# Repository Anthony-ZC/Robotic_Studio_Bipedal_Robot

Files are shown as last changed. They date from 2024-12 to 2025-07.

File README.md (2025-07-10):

# Robot Studio: Bipeda Robot Full Project Implementation  
It is a bipedal robot implementation for **Columbia MECE 4611 Robotics Studio (Fall 2024)** created by ***Zewen "Anthony" Chen*** and ***Xinhe "Carl" Yang*** . We get inspiration by Yuhang Hu's work [CB-20](https://www.youtube.com/watch?v=Y0fBdpLf9ZI&t=1s) and redesign it.

---

### Say Beforehand

For those who attend Robotics Studio in the future or want to build their own first bipedal robot, I hope this implementation can help you. But remember, it is far from perfect. Here are drawbacks and suggestions for improvement:
1. It is relatively heavy, the whole weight reaches close to 1.5 kg. and the weight is not concentrated enough, if you can lighten it and concentrate the mass it should be able to run faster. I think under 1.2kg would be ideal.
2. The fact that we don't have the two motors located in the hip joints due to timing issues results in extra weight. If you can make the most of them, the robot should be able to make more gaits and be more stable.
3. Due to the parallel design of the legs, they are compressed by their own weight and can not be considered as rigid bodies, which makes simulation to reality more difficult, improving the design or replacing the other structures may improve.

### <u>**So, do not just copy it, make it better!**</u>  

Best wishes,  
Anthony Chen  

---

### Project Overview

- **Project Video**  
  - [x] Playlist Link: [https://www.youtube.com/playlist?list=PLH_mFWdIEgZGXP19iW7NsymILhA3eG9Pi](https://www.youtube.com/playlist?list=PLH_mFWdIEgZGXP19iW7NsymILhA3eG9Pi)  
  - [x] Journey Video:  
  
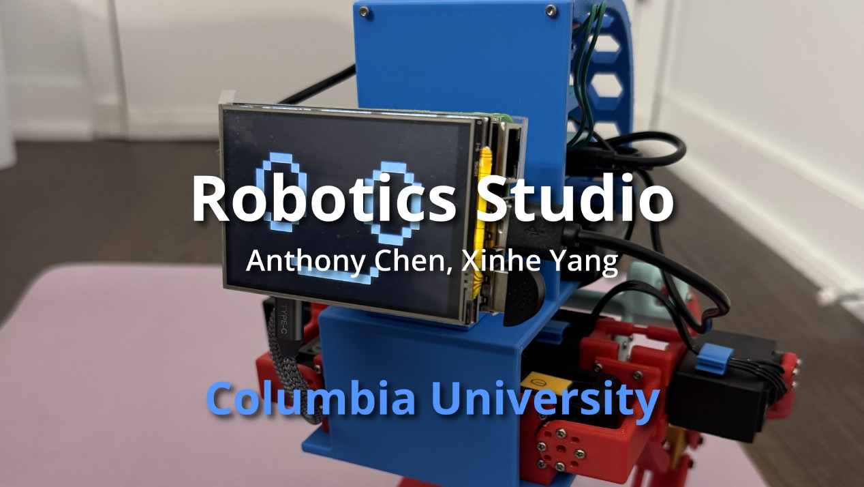
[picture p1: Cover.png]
Watch the video (https://www.youtube.com/watch?v=UUYPjQSJz8M)
 

- **CAD**  
  - [x] CAD Link (GrabCAD): [https://grabcad.com/library/robotics-studio-bipedel-robot-1](https://grabcad.com/library/robotics-studio-bipedal-robot-1)  

- **3D Printing**  
  - [x] [STL Files](./3D%20Printing/)  
  - [x] MarkerWorld Link: [https://makerworld.com/zh/models/903789#profileId-863432](https://makerworld.com/zh/models/903789#profileId-863432)  

- **Assembly Guidance**  
  - [x] [Purchase Links for Essential Parts](#purchase-links-for-essential-parts)  
  - [x] [Additional Assembly Information](#additional-assembly-information) **$${\color{red}\enspace It \enspace contains \enspace many \enspace important \enspace lessons \enspace from \enspace my \enspace experience,\enspace so\enspace be\enspace sure\enspace to\enspace check\enspace them\enspace out!}$$**
  - [ ] Assembly Video in CAD  
  Probably won't do it anytime soon, I think a good robotics engineer should be capable of analyzing and assembling this robot (or just because I am lazy ╮(╯▽╰)╭). But if enough requests are posted in issues, perhaps I'll make it.

- [**Control**](#control)
  - [x] [Requirements](#requirements)
  - [x] [Testing Code](#testing-code)
  - [x] [Servo Curve Analysis](#servo-curve-analysis)
  - [x] [Integrated Control Code](#integrated-control-code)

- [**Simulation**](#simulation)
  - [x] [Extra Requirements](#extra-requirements)
  - [x] [Equivalent Series Structure Simplification](#equivalent-series-structure-simplification)
  - [x] [STL & URDF](#stl--urdf): 
  [12cm Upeer Legs](./Simulation/model/) 
  [8cm Upeer Legs](./Simulation/model8/)
  - [x] [Simulation Code](#simulation-code)
---
### Assembly Guidance
#### Purchase Links for Essential Parts
- **Amazon**  
  - <u>**7★**</u> [LX-16A Serial Bus Servo](https://www.amazon.com/LewanSoul-Real-Time-Feedback-Bearing-Brackets/dp/B0748BQ49M) (Singal Servo)
  - <u>**1★**</u> [LX-16A Serial Bus Servo Controller](https://www.amazon.com/LewanSoul-BusLinker-Debug-Board-LX-16A/dp/B073WRLJB2?ref_=ast_sto_dp)
  - <u>**Extra**</u>[5 Packs LX-16A Serial Bus Servo with Servo Controller Kits](https://www.amazon.com/Hiwonder-LX-16A-Robotic-Controller-Control/dp/B073XY5NT1) (You can buy servos and controller separately or this kit and 2 extra servos.)
  - <u>**1★**</u> [Battery Pack](https://www.amazon.com/dp/B01M7Z9Z1N) (You may use any other battery have DC 12V/5V USB dual output.)  
  **$${\color{red}Warning:}$$** **This battery may not be able to afford more than 8 servos.**
  - <u>**1★**</u> [DC to DC Converter](https://www.amazon.com/gp/product/B00BYS9JYA)
  - <u>**1★**</u> [Raspberry Pi 4](https://www.amazon.com/Raspberry-Model-2019-Quad-Bluetooth/dp/B07TD42S27?th=1)
  - <u>**1★**</u> [Micro SD Card ](https://www.amazon.com/dp/B073JWXGNT?th=1)
  - <u>**1★**</u> [USB Male to USB C](https://www.amazon.com/Braided-Compatible-Samsung-Portable-Charger/dp/B07HQHL6ZK?th=1)
  - <u>**1★**</u> [Raspberry Pi Touch Screen](https://www.amazon.com/dp/B0D4DL38MF?ref=ppx_yo2ov_dt_b_fed_asin_title)  
 **$${\color{red}Warning:}$$** **Please follow the driver installation guidance in the product description to enable it on Raspberry Pi. You may not be able to use  <u>HDMI</u> output if you enable the touchscreen. If the touchscreen does not work, please delete "LCD- show" floder and install it again.**
  - <u>**1**</u> [USB 2.0 Mini Microphone](https://www.amazon.com/dp/B071WH7FC6?ref=ppx_yo2ov_dt_b_fed_asin_title)
  - <u>**1 pkg**</u> [Raspberry Pi 4 Heatsink](https://www.amazon.com/dp/B0963BMGFY?ref=ppx_yo2ov_dt_b_fed_asin_title) (The 4mm-thick heatsink in it is perfectly adapted to the touchscreen.)
  - <u>**1 pkg**</u> [M2 M3  Male Female Hex Brass Standoffs Spacers Screws Nuts Kit](https://www.amazon.com/dp/B06XCNF6HK?ref=ppx_yo2ov_dt_b_fed_asin_title&th=1) (We only use M2 here.)
  - <u>**1 pkg**</u> [M3x6mmx0.5mm Stainless Steel Round Flat Washer](https://www.amazon.com/dp/B015A39NCC?ref=ppx_yo2ov_dt_b_fed_asin_title) (You may use any other 3mm flat washer with aorund 0.5mm thicknesses.)

- **AliExpress**  
  - <u>**8 pcs**</u> [3x16xM2 Shoulder Screw ](https://www.aliexpress.us/item/3256806009271581.html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)

- **McMaster**  
  - <u>**1 pkg★**</u> [M2 x 0.4 mm Thread, 8 mm Long, Stainless Steel Socket Head Screw](https://www.mcmaster.com/91292A832/)  
  - <u>**1 pkg★**</u> [M2 x 0.4 mm Thread, 12 mm Long, Stainless Steel Socket Head Screw](https://www.mcmaster.com/91292A834/)
  - <u>**1 pkg★**</u> [M2 x 0.4 mm Thread Size, 2.9 mm Installed Length, Brass Tapered Heat-Set Inserts for Plastic](https://www.mcmaster.com/94180A307/)  
  - <u>**2 pkg**</u> [for Plastic, 18-8 Stainless Steel, M2.2 Screw Size, 8 mm Long, Phillips Rounded Head Thread-Forming Screws](https://www.mcmaster.com/99461A922/)  
  - <u>**1 pkg**</u> [for M2 Screw Size, Standard, 2.4 mm ID, 4.4 mm OD, 18-8 Stainless Steel Split Lock Washer](https://www.mcmaster.com/92148A050/)  
  - <u>**1 pkg**</u> [Medium-Strength, Class 8, M2 x 0.4 mm Thread, Zinc-Plated Steel Hex Nut](https://www.mcmaster.com/90591A265/)  
  - <u>**4 pcs**</u> [3 mm Shoulder Diameter, 25 mm Shoulder Length, M2 x 0.4 mm Thread Alloy Steel Shoulder Screws](https://www.mcmaster.com/92981A775/)
 
★ This item will be included in the lecture kit if you attend Columbia MECE 4611 Robotics Studio. 
#### Additional Assembly Information 
  - For 3D-printed ***"Robot_Cover"*** part, you need to do **thermal insert** through the soldering iron.
  - For ***"Cylinder_Pi"*** and ***"Cylinder_DC_Converter"*** parts in CAD, **do not 3D print it**, use [M2 studs](https://www.amazon.com/dp/B06XCNF6HK?ref=ppx_yo2ov_dt_b_fed_asin_title&th=1) above instead. I have tried 3D print studs with thermal inserts but failed, that's why they are not included in 3D Printing files.
  - In Solidworks CAD, you may see **Internal-Tooth Lock Washer** for mating convenience in Solidworks. However, you can use other less damaging lock washers like [Split Lock Washer](https://www.mcmaster.com/92148A050/) instead.
  - For ***"Raspberry_Pi_Platform"*** part, you can use **laser cut acrylic sheets** to get it instead of 3D printing
  - Although the screws that connect the ***"Raspberry Pi"***, the ***"Raspberry_Pi_Platform"***, the ***"Servo_Connector_Head"***, and the ***"studs that hold the DC converter"*** in place in CAD do not use a **lock washer,** it is highly recommended that you use one in order to prevent parts from falling out of place during the robot's motion.
  - Although the 8cm shorter upper legs are included in this project and the [simulation](https://youtu.be/Yh0ZwXFP5J8?si=DioH9wF-7lgsMUER) shows it somehow better, I failed to make the robot walk using them. But, you can try.
> [!Caution]
> **Very Important!:**  Make sure you print two legs using **same kind of filament** (say do not print the left leg with PLA basic and right leg with PLA matte, or even filaments from different brands), or the robot might hard to balance (like [this](https://youtu.be/c0_l959v7TQ?si=rPd1EVJWCl6EjpbT)).

> [!Note]
>  You may see parts in the CAD model that do not mate well, such as the screw holes for the DC converter, this is because these parts have been updated and we were unable to find the latest CAD file and had to use a similar CAD. therefore, we strongly recommend that you measure them before printing. The following parts are the ones you need to focus on:
>   1. Servo size and screw spacing (although we were lucky enough to find the official CAD file and confirm that it correctly points out all the dimensions, but just in case)
>   2. Battery size
>   3. DC converter screw hole spacing (we measured with electronic vernier calipers and the print should be in compliance, but it is still recommended that you measure again)
>   4. Servo controller dimensions and board thickness (be sure to re-measure the servo controller retainer if you want to redesign its holder)
---

### Control  
#### Requirements
 - Python 3.10.15+ (To install PyLX-16A package, you must use a Python environment with 3.10 or newer version.)
 - [PyLX-16A](https://github.com/ethanlipson/PyLX-16A/tree/master) 
 - Numpy 2.1.3+
 - Pyserial 3.5+
 - PyQt6 6.7.1+ (for visual debugging on windows, **cannot process on RasoberryPi**)
 - SpeechRecognition (for voice recognition)
 - Pygame (for screen facial expression)
#### Testing Code
 - [**servo-test.py**](./Control/servo-test.py)  
    Visualized servo adjusting code.
 - [**test_hello-world.py**](./Control/test_hello-world.py)  
    3 servos sinusoidal testing code.
#### Servo Curve Analysis
 - [**servo_curve_visualization.py**](./Control/servo_curve_visualization.py)  
    By setting the walk period and servo keyframes, you can plot the servo angle curves of preparation phase, periodic walk phase, and stop phase obtained by cubic polynomial interpolation. Accordingly you can check the servos for excessive overshooting and thus avoid violent shaking or damage to the robot. 

The robot in this project uses a keyframe + cubic polynomial interpolation approach for periodic gait planning, taking into account the smooth transitions required for start and termination. This formula ensures continuity of servo position, velocity and acceleration throughout the robot's travel. A simple explanation of the idea is shown in the figure below:
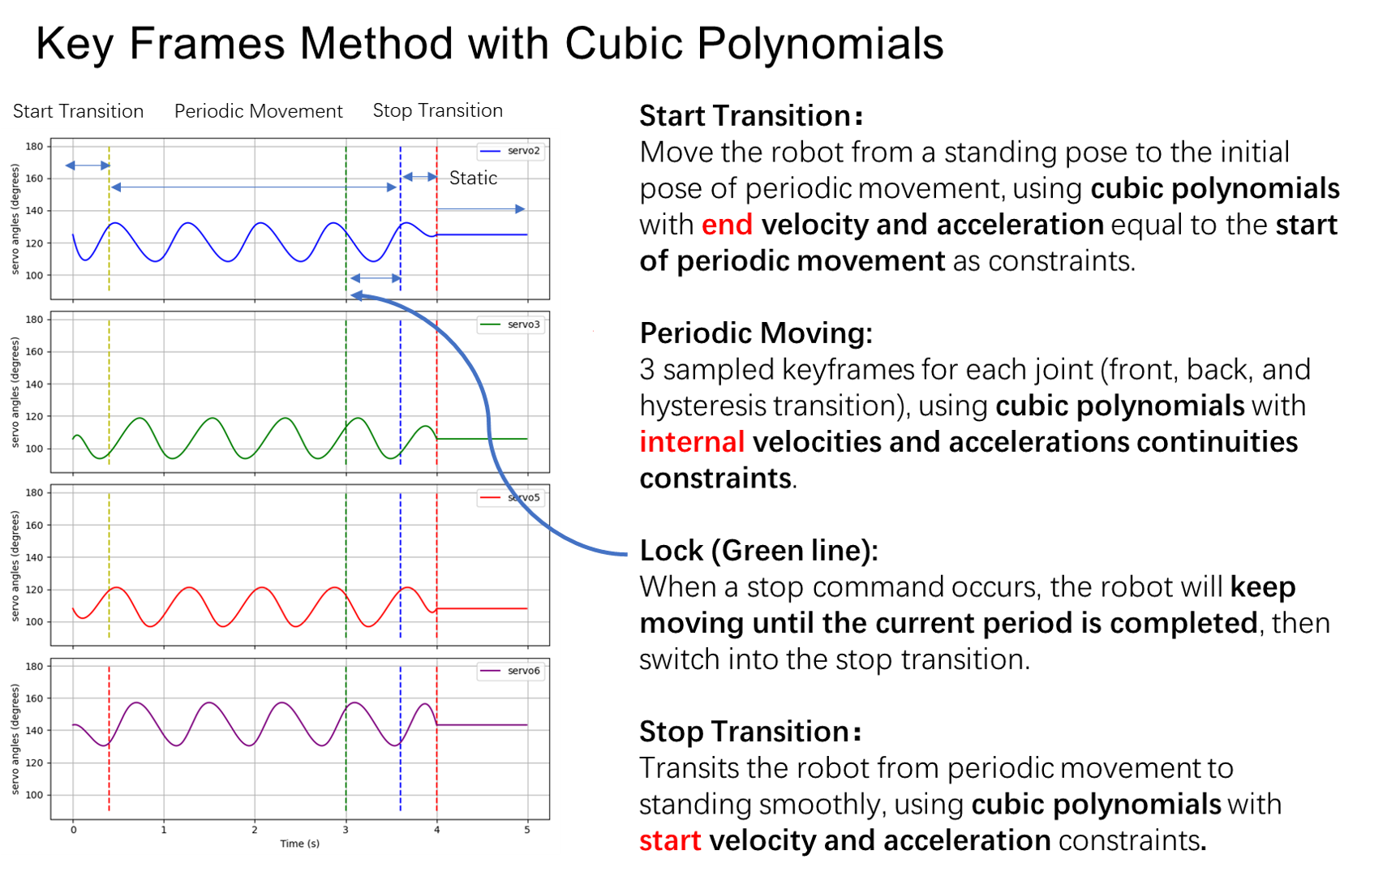
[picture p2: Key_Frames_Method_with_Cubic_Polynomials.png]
Key Frames

For this project I used linear equations to solve for multiple cubic polynomial coefficients simultaneously, which you should be familiar with if you also took the Columbia MECS 4603 AppliedRobotics: Algorithm & Software course. This method would be included in "Trajectory Execution" part.
#### Integrated Control Code
The integration control code is essentially designed to run on a Raspberry Pi although it can also be used by connecting the servo controller usb cable to a computer. Therefore, before you use this integrated control code, **it is highly recommended that you learn how to control the Raspberry Pi wirelessly using Remote Desktop.** You can follow this video 👉 [Raspberry Pi Headless Setup](https://youtu.be/dhY8m_Eg5iU?si=XMZ2caKZ6iJjB2I0) to install xrdp on Raspberry Pi and use **Windows Remote Connection** on the laptop.

 - [**Robot.py**](./Control/Robot.py)  

This integrated control code is used to provide basic control of the project's bipedal robot. It includes the following main functions:  
1. Wake up the robot, control the robot to switch between homing and standing poses
2. Nodding and Squatting
3. Periodic walking using a cubic polynomial with smooth transitions for starting and stopping.
4. Control the robot using terminal input or voice (microphone required).
5. Display corresponding facial expressions on the Raspberry Pi touchscreen according to different commands.
6. Periodic servo health check (position, temperature, voltage).  
    
> [!Warning]
> - Since the facial expressions was originally intended to be on a Raspberry Pi touchscreen, pygame's output screen number is specified as 0. However, if you use Remote Desktop to launch the Facial Expression feature on a Raspberry Pi **without** connecting a touchscreen, the Facial Expression display may be redirected to the Remote Desktop and paralyze it. Therefore, please disable this funtion when you are not using a touchscreen on your robot.
>   ```
>    robot = Robot(7, 'keyboard', False)
>   ```

> [!Note]
> - Since voice input has only been tested on the Raspberry Pi, there is no guarantee that this feature will work properly when connected to a computer.
> - The servo angles in the code are intended to be applied to the original size (12cm) upper leg, if you plan to use a shorter 8cm upper leg, please re-measure the servo angle.
---
### Simulation  
#### Extra Requirements
 - Visual Studio 2022+ (for supporting pybullet simulation)
 - Pybullet 3.2.6+ (for simulation)
#### Equivalent Series Structure Simplification
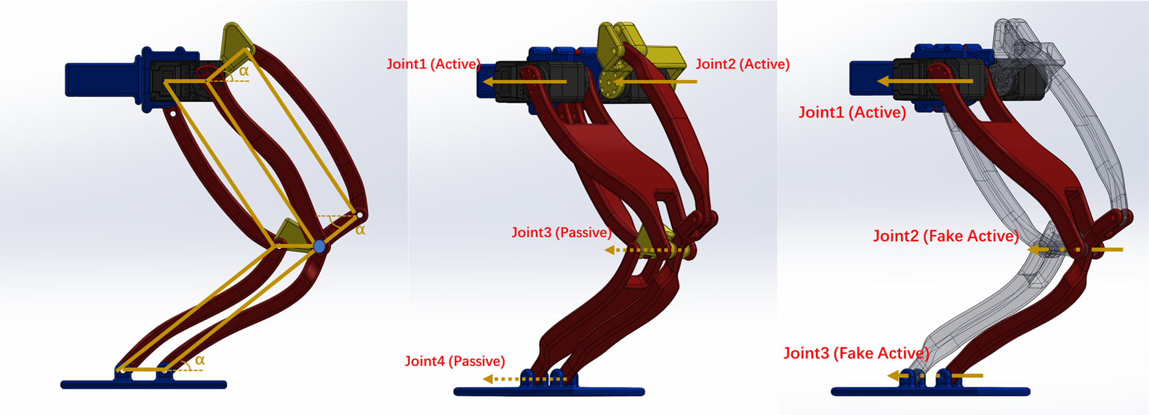
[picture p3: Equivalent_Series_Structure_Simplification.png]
Explanation Image

The top left image shows the parallel linkage structure of the legs, where the robot's legs actually consist of three parallelograms. The three angles (α) shown in the image are equal.
Thus, we can simplify the original active and multiple passive joints shown in the center image above to the series structure shown in the right image above (the translucent parts are suppressed).
The joint angle Equivalent Series Structure Simplification has following relationship:
- Joint1(Active) remains unchanged.
- Joint2(Fake Active) equals original Joint2(Active).
- Joint3(Fake Active) equals to the negative of Joint1(Active)+Joint2(Fake Active), which mimics the original parallel construction making the foot always parallel to the base.
#### STL & URDF
- In the "Simulation" folder, I provide 2 URDF files and the associated STL files. The "model" folder is for the original size upper leg (12cm) and the "model8" folder is for the short upper leg (8cm). 
- In URDF, for the inertial parameters of the links, the weight was measured by weighing each part individually on an electronic scale with an accuracy of 1g, and the center of mass and inertia were measured by using Mass Properties in the Solidworks Evaluate option. Due to possible variations in the print material, I recommend that you reweigh the individual parts of your robot.
- You can see my definition of the coordinate system and key rotation axes in the SLDASM assembly files with "for_simulation" suffixes in [GrabCAD](https://grabcad.com/library/robotics-studio-bipedal-robot-1) .
#### Simulation Code
In all simulation codes, models of different lengths of upper legs were loaded by  
original size (12cm):
```
robotId = p.loadURDF("model\myrobot_series.urdf",robotStartPos, robotStartOrientation,useFixedBase=False)
```
short size (8cm):
```
robotId = p.loadURDF("model8\myrobot_series.urdf",robotStartPos, robotStartOrientation,useFixedBase=False)
```
In Pybullet, you can use **ctrl+left mouse button** to rotate the view or **ctrl+middle mouse button** to pan the view. Also, if you want to fix the robot in the air for further observation, please make the following settings:
```
robotId = p.loadURDF("model\myrobot_series.urdf",robotStartPos, robotStartOrientation,useFixedBase=True)
```
 - [**basic_simu.py**](./Simulation/basic_simu.py)
 The code provides the most basic simulation functionality for loading the ground with robots.
 - [**sin_walk.py**](./Simulation/sin_walk.py)
 This code provides the ability to drive the robot to walk using a single sinusoidal curve, which will output the average linear velocity at the endpoints.
 - [**cubic_walk.py**](./Simulation/cubic_walk.py)
 This code provides the ability to drive the robot to walk using the same cubic polynomial curve as in the control code, and will output the average line speed at the terminal.
 - [**jump.py**](./Simulation/jump.py)
 The code provides the ability to drive a robot to jump using an unequal amplitude sinusoidal signal, which works better in the short upper legs model.

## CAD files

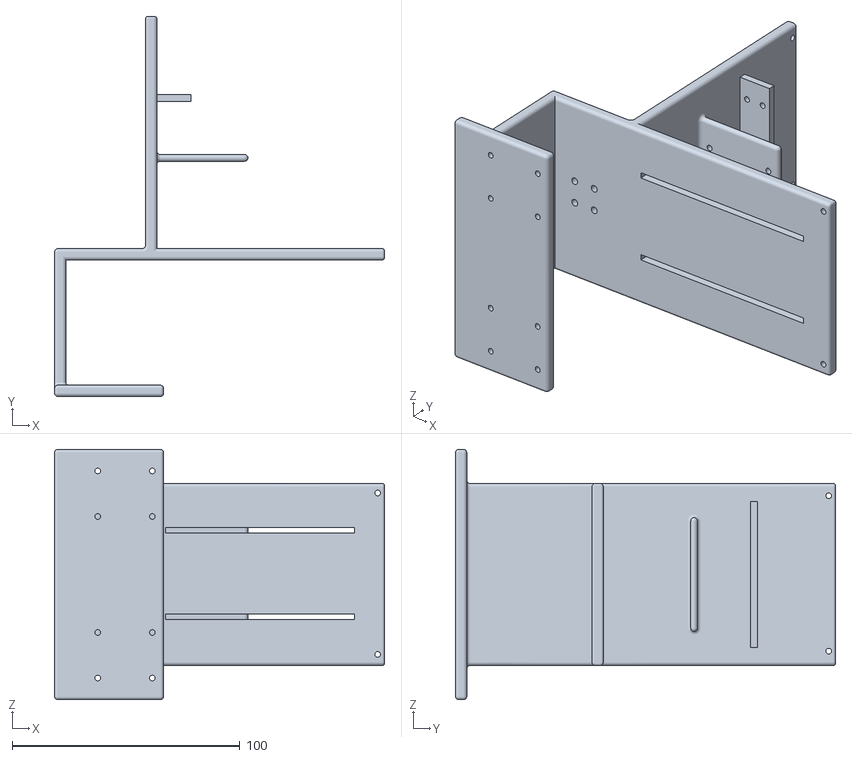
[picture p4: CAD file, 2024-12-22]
3D Printing/Base/Base_Platform.STL
145.0 x 167.0 x 110.0

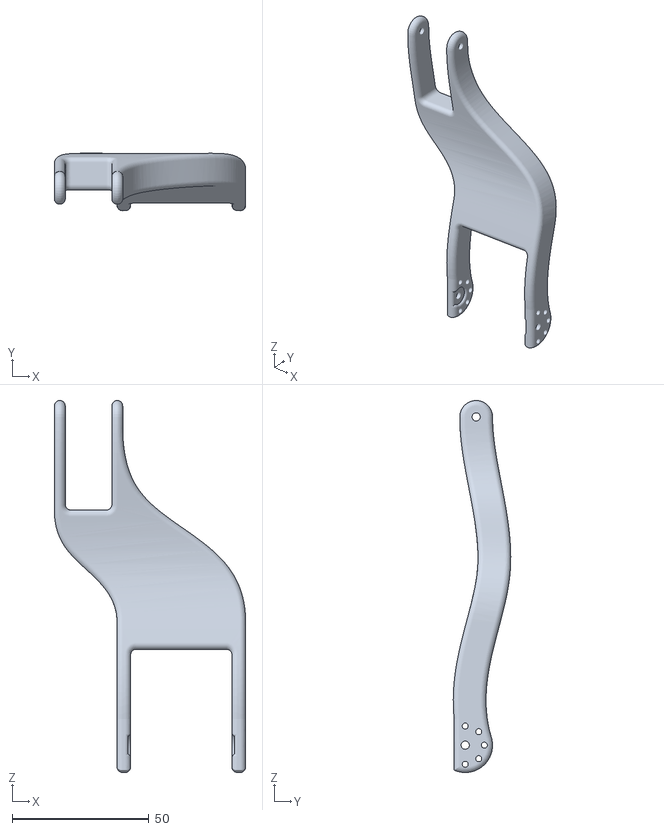
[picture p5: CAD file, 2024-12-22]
3D Printing/Leg/Leg_Upper_Middle_Right.STL
69.9 x 21.0 x 135.9

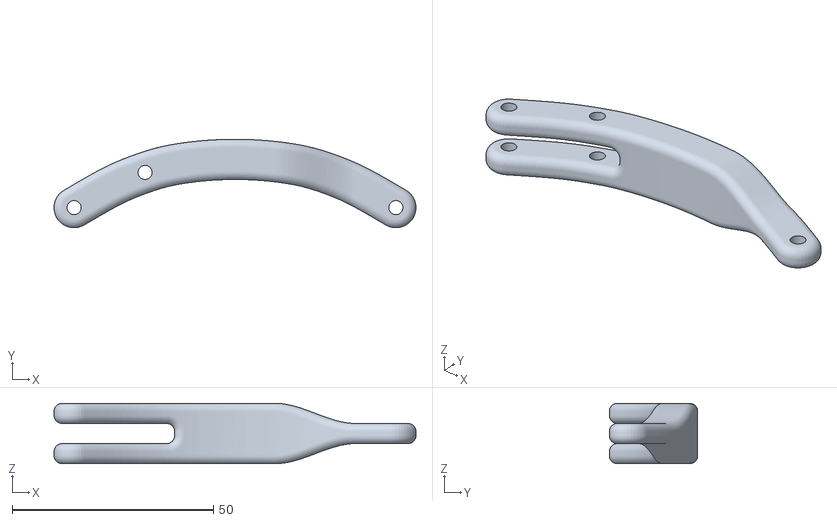
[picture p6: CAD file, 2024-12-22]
3D Printing/Short Upper Leg/Leg_Upper_Back_8.STL
90.0 x 22.0 x 15.0

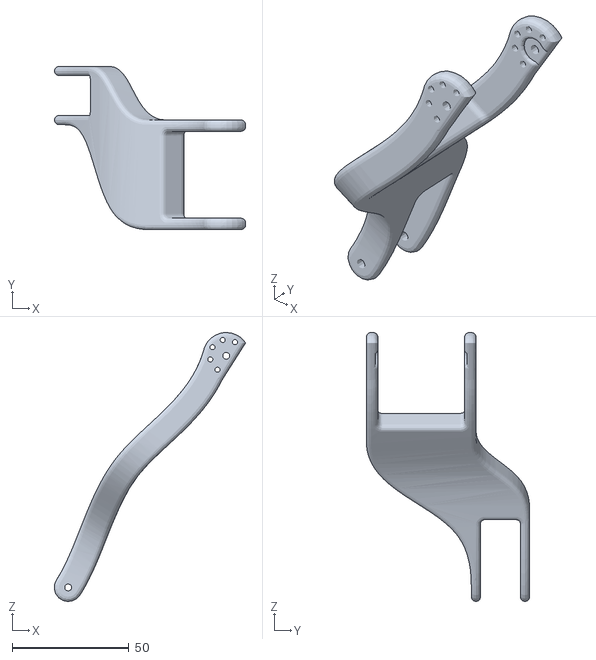
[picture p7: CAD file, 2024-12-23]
Simulation/model/Right_Upper_Middle.STL
81.9 x 69.9 x 115.1

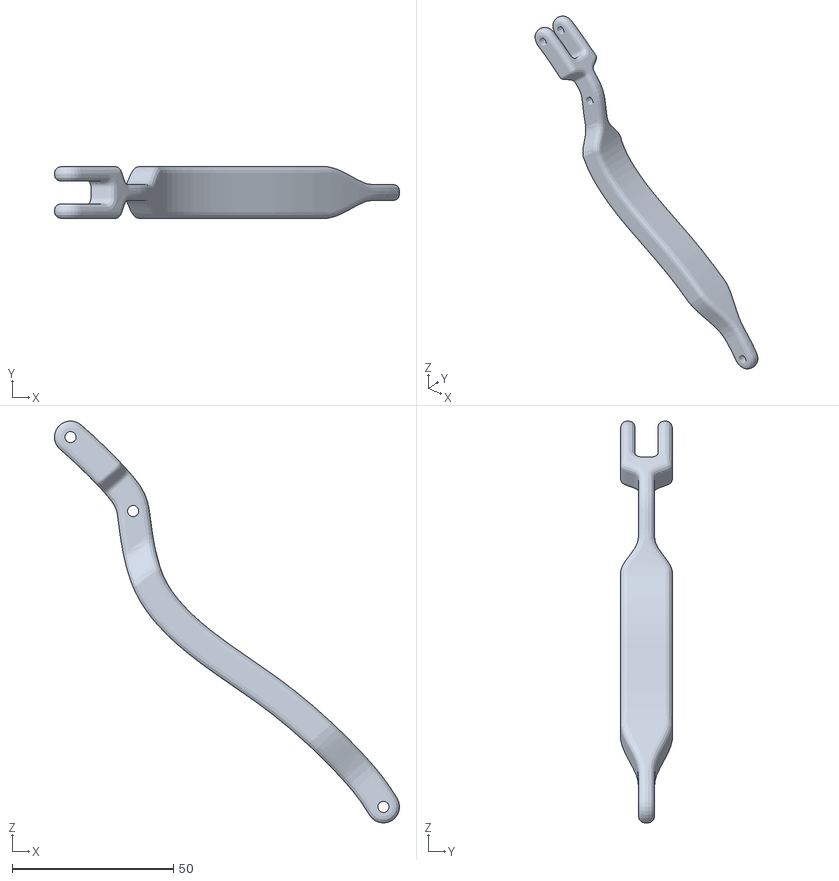
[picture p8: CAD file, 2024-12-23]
Simulation/model8/Right_Lower.STL
106.9 x 16.0 x 124.5

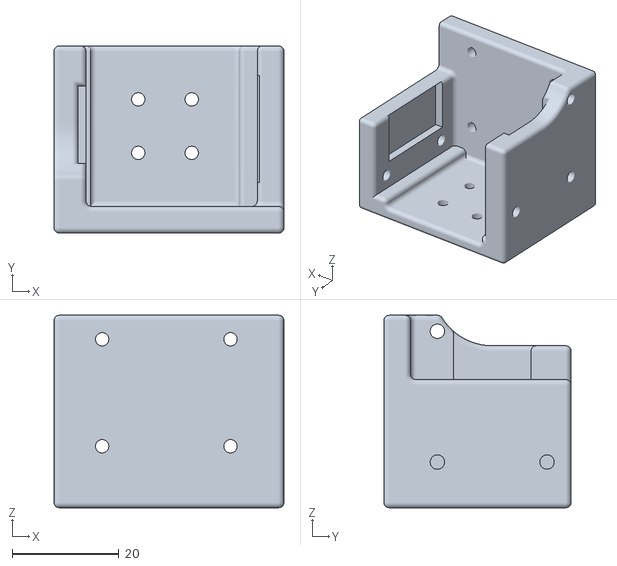
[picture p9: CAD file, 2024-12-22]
3D Printing/Base/Servo_Fixture_Head.STL
43.0 x 35.0 x 36.0

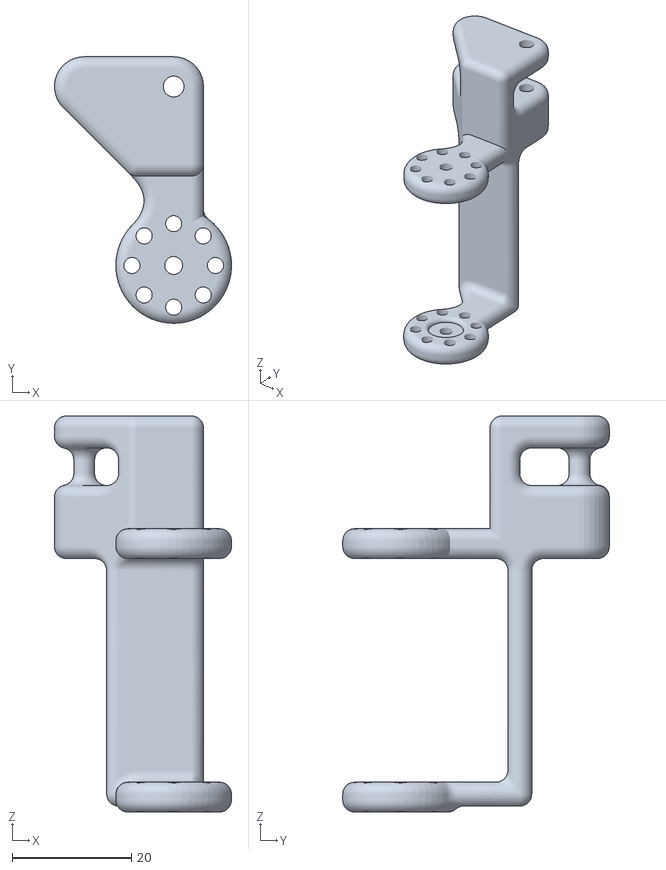
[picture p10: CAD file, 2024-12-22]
3D Printing/Leg/Connector1_left.STL
29.7 x 44.7 x 66.4

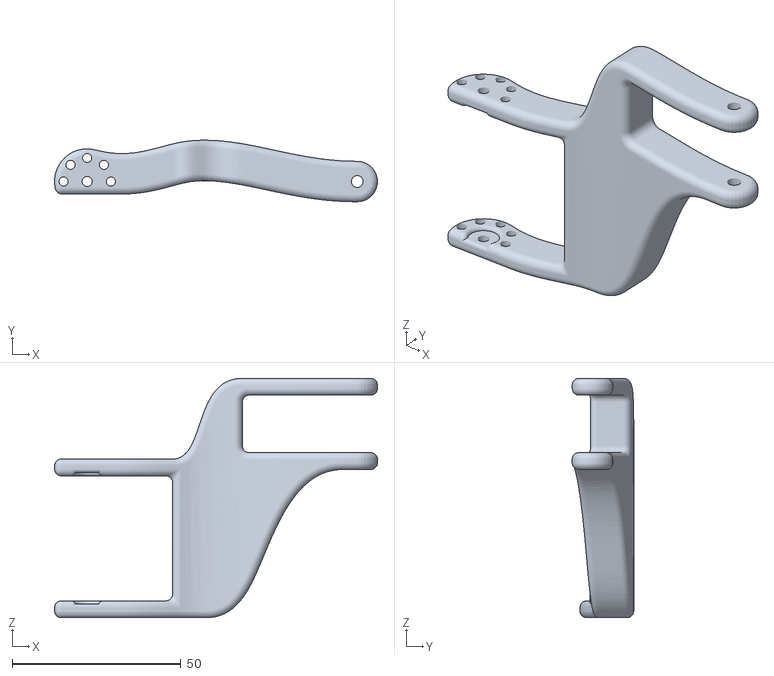
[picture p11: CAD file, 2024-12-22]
3D Printing/Short Upper Leg/Leg_Upper_Midddle_8_Right.STL
95.7 x 18.3 x 70.9

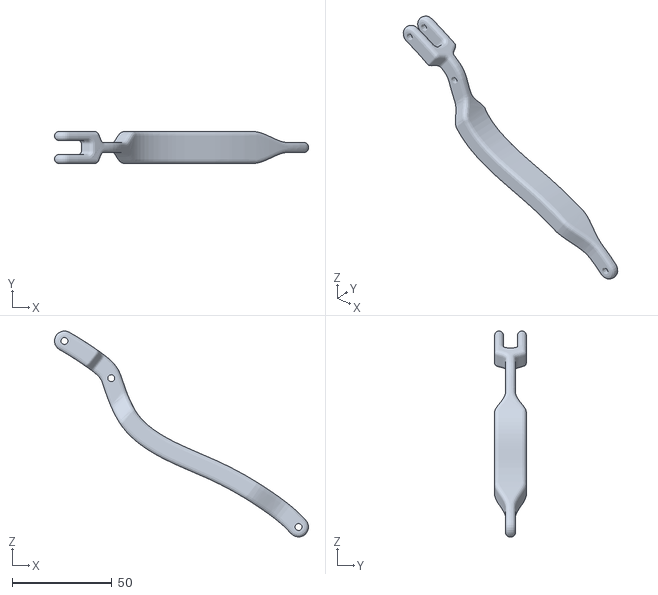
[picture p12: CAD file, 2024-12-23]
Simulation/model/Right_Lower.STL
127.4 x 16.0 x 103.3

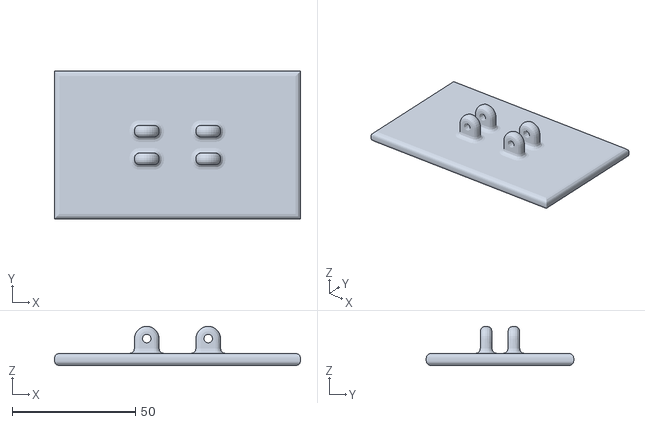
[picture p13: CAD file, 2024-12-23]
Simulation/model8/Left_Feet.STL
100.0 x 60.0 x 16.0

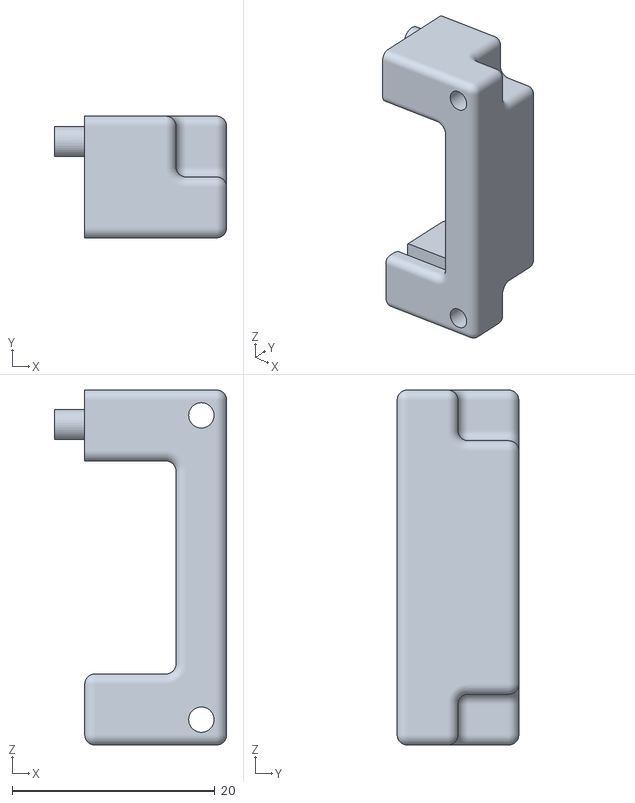
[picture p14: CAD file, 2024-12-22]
3D Printing/Base/Controller_Case2.STL
17.0 x 12.0 x 35.0

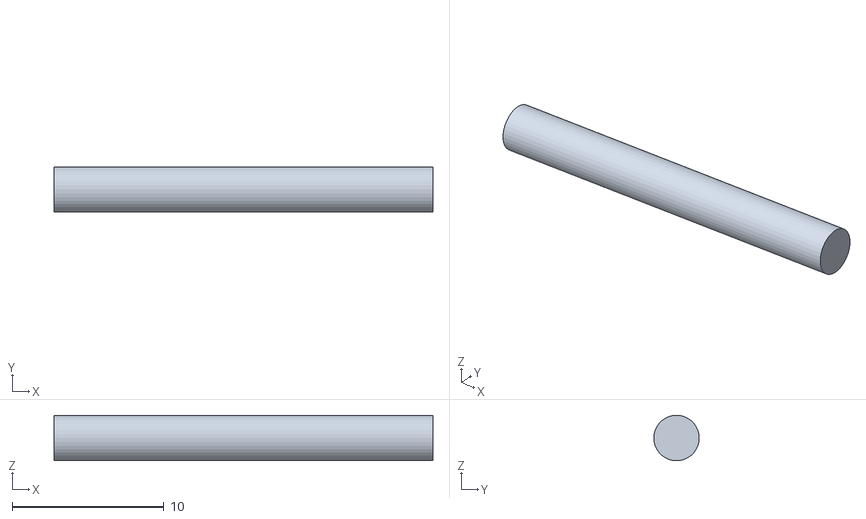
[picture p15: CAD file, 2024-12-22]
3D Printing/Leg/Shaft2.STL
25.0 x 3.00 x 3.00

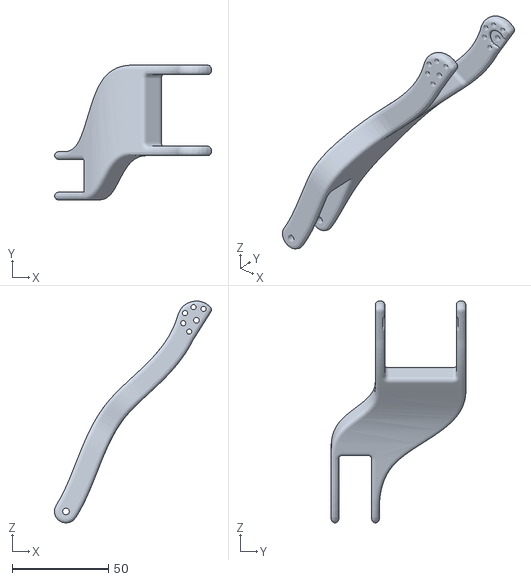
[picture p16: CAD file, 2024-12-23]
Simulation/model/Left_Upper_Middle.STL
81.4 x 69.9 x 115.1

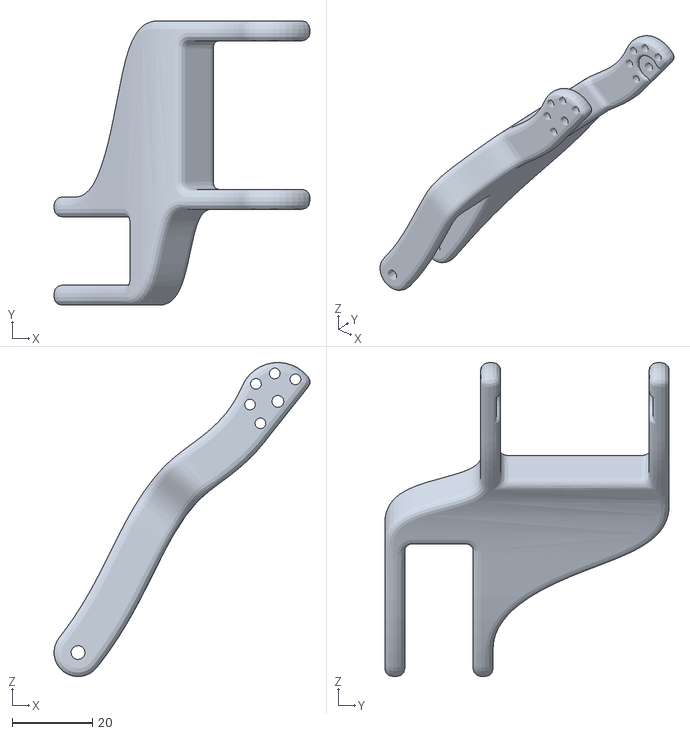
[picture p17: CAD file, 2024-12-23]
Simulation/model8/Left_Upper.STL
63.8 x 70.9 x 78.3

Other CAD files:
3D Printing/Short Upper Leg/Leg_Upper_Midddle_8_Left.STL
3D Printing/Base/Battery_Holder.STL
3D Printing/Leg/Connector1_right.STL
3D Printing/Short Upper Leg/Leg_Upper_Front_8.STL
3D Printing/Base/Base_Modulous.STL
3D Printing/Base/Controller_Case1.STL
3D Printing/Base/Raspberry_Pi_Platform.STL
3D Printing/Base/Robot_Cover.STL
3D Printing/Base/Servo_Connector_Head.STL
3D Printing/Leg/Connector2.STL
3D Printing/Leg/Feet_10x8.STL
3D Printing/Leg/Feet_8x4.STL
3D Printing/Leg/Leg_Lower_Back.STL
3D Printing/Leg/Leg_Lower_Front.STL
3D Printing/Leg/Leg_Upper_Back.STL
3D Printing/Leg/Leg_Upper_Front.STL
3D Printing/Leg/Leg_Upper_Middle_Left.STL
3D Printing/Leg/Servo_Connector_Leg.STL
3D Printing/Leg/Servo_Fixture_Hip_Left.STL
3D Printing/Leg/Servo_Fixture_Hip_Right.STL
3D Printing/Leg/Servo_Fixture_Leg.STL
3D Printing/Leg/Servo_Fixture_Leg_Mirror.STL
3D Printing/Leg/Shaft1.STL
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

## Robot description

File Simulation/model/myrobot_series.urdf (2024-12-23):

<?xml version="1.0"?>
<robot name="myrobot">
    <link name="base">
        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

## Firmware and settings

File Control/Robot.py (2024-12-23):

from math import sin, cos, ceil
from pylx16a.lx16a import *
import time,os
import numpy as np
import threading
from copy import deepcopy
import pygame
import speech_recognition as sr

def cubic_polynomial(ps,ts,extra_velocity_constraint,extra_acceleration_constraint,constraint_type = 'end'):
    """
    Calculate the cubic polynomial coefficients for the given waypoints and time stamps and constraints, which ensures the continuity of the velocity and acceleration at the waypoints.
    Extra zero constraints are added to the velocity and acceleration at the end or start of the waypoints.
    Solution is obtained by solving a linear system of equations.
    
    Args:
        ps (list): list of waypoints
        ts (list): list of time stamps
        extra_velocity_constraint (float): extra velocity constraint
        extra_acceleration_constraint (float): extra acceleration constraint
        constraint_type (str): constraint type, 'end' or 'start', for 'start' constraint, the first velocity and acceleration are constrained, for 'end' constraint, the last velocity and acceleration are constrained.

    Returns:
        cubic polynomial coefficients (numpy.ndarray): cubic polynomial coefficients
    """
    assert len(ps) == len(ts)+1
    
    n = len(ps)-1
    A =  np.zeros((n*4,n*4))
    
    # Position constraints
    for i in range(n):
        j = i
        A[i*2,j*4] = A[i*2,j*4+1] = A[i*2,j*4+2] = 0
        A[i*2,j*4+3] = 1

        A[i*2+1,j*4] = ts[j]**3
        A[i*2+1,j*4+1] = ts[j]**2
        A[i*2+1,j*4+2] = ts[j]
        A[i*2+1,j*4+3] = 1
    # Velocity constraints
    for i in range(2*n,3*n-1):
        j = i -2*n
        A[i,j*4] = 3 * ts[j]**2
        A[i,j*4+1] = 2 * ts[j]
        A[i,j*4+2] = 1
        A[i,j*4+6] = -1
    # Acceleration constraints
    for i in range(3*n,4*n-1):
        j = i -3*n
        A[i,j*4] = 6 * ts[j]
        A[i,j*4+1] = 2 
        A[i,j*4+5] = -2
    
    # Waypoints' position
    y =  np.zeros((n*4,1))
    y[0] = ps[0]
    y[2*n-1] = ps[-1]
    for i in range(len(ps)-2):
        y[2*i+1] = y[2*i+2] = ps[i+1]
        
    # Extra constraints
    if constraint_type == 'end':
        A[3*n-1,4*n-4] = 3 * ts[n-1]**2
        A[3*n-1,4*n-3] = 2 * ts[n-1]
        A[3*n-1,4*n-2] = 1
        A[4*n-1,4*n-4] = 6 * ts[n-1]
        A[4*n-1,4*n-3] = 2
    elif constraint_type == 'start':
        A[3*n-1,2] = 1
        A[4*n-1,1] = 2

    y[3*n-1] = extra_velocity_constraint
    y[4*n-1] = extra_acceleration_constraint

    return np.linalg.inv(A) @ y


def cubic_polynomial_periodic(ps,ts):
    """
    Calculate the cubic polynomial coefficients for the given waypoints and time stamps, which ensures the continuity of the velocity and acceleration at the waypoints.
    Boundary conditions are periodic, which means the velocity and acceleration at the end and start of the waypoints are equal.
    Solution is obtained by solving a linear system of equations.

    Args:
        ps (list): list of waypoints
        ts (list): list of time stamps

    Returns:
        cubic polynomial coefficients (numpy.ndarray): cubic polynomial coefficients
    """
    assert len(ps) == len(ts)+1
    
    n = len(ps)-1
    A =  np.zeros((n*4,n*4))

    # Position constraints
    for i in range(n):
        j = i
        A[i*2,j*4] = A[i*2,j*4+1] = A[i*2,j*4+2] = 0
        A[i*2,j*4+3] = 1

        A[i*2+1,j*4] = ts[j]**3
        A[i*2+1,j*4+1] = ts[j]**2
        A[i*2+1,j*4+2] = ts[j]
        A[i*2+1,j*4+3] = 1

    # Velocity constraints
    for i in range(2*n,3*n-1):
        j = i -2*n
        A[i,j*4] = 3 * ts[j]**2
        A[i,j*4+1] = 2 * ts[j]
        A[i,j*4+2] = 1
        A[i,j*4+6] = -1

    A[3*n-1,2] = -1
    A[3*n-1,4*n-4] = 3 * ts[n-1]**2
    A[3*n-1,4*n-3] = 2 * ts[n-1]
    A[3*n-1,4*n-2] = 1

    # Acceleration constraints
    for i in range(3*n,4*n-1):
        j = i -3*n
        A[i,j*4] = 6 * ts[j]
        A[i,j*4+1] = 2 
        A[i,j*4+5] = -2

    A[4*n-1,1] = -2
    A[4*n-1,4*n-4] = 6 * ts[n-1]
    A[4*n-1,4*n-3] = 2
    
    # Waypoints' position
    y =  np.zeros((n*4,1))
    y[0] = ps[0]
    y[2*n-1] = ps[-1]
    for i in range(len(ps)-2):
        y[2*i+1] = y[2*i+2] = ps[i+1]
        
    return np.linalg.inv(A) @ y

class ServoError(Exception):
    '''
    Exception raised for errors in the servo.
    '''
    def __init__(self, message):
        self.message = message
 
    def __str__(self):
        return self.message


class Robot:
    '''
    Robot class for controlling the robot.
    '''
    def __init__(self, servo_num,control_mode = 'keyboard', enable_face = False):
        '''
        Initialize the robot.
        
        Args:
            servo_num (int): number of servos
            control_mode (str): control mode, 'keyboard' or 'mic'
            enable_face (bool): enable face or not
        '''

        # Initialize the servos
        try:
            # Raspberry Pi
            LX16A.initialize("/dev/ttyUSB0", 0.1)
        except:
            # Windows
            LX16A.initialize("/COM6", 0.1)

        self.servo_num = servo_num
        self.q = [0]*self.servo_num
        self.servo_status = [[False, False, False] for i in range(self.servo_num)]

        # Set the limits for the servos' voltage, temperature, and angle
        self.voltage_lower_limit = 4500
        self.voltage_upper_limit = 12000
        self.temperature_limit = 70
        self.angle_lower_limit = 0
        self.angle_upper_limit = 240

        # Initialize the robot command
        self.robot_command = ''
        self.exiting = False

        # Initialize the head and leg status
        self.leg_status = None
        self.head_status = None

        # Initialize the walk parameters
        self.walk_prepare_time = 0
        self.walk_stop_time = 0
        self.walk_2_stop = False
        self.walk_wait_time = 0
        
        # Initialize the timer and time
        self.start_time = time.time()
        self.time_stamp = time.time()
        self.running_time = 0
        self.check_period = 10
        # timer1 for head movement, timer2 for leg movement
        self.timer1 = 0
        self.timer2 = 0

        # Initialize the main loop parameters
        # time for long time operation
        self.mian_proceed_time = 2
        # time for each step
        self.main_step_time = 0.1
        # time for each sleep
        self.main_sleep_time = 0.05

        # Initialize the pose for homing and standing up
        self.pose_homing = [114, 94.48, 95.76, 116.64, 137.76, 151.68, 100]
        self.pose_stand_up = [114, 120, 104, 116.88, 108, 148, 100]

        # Initialize the cubic polynomial coefficients for the walk
        self.curve_properties = [{} for i in range(self.servo_num)]
        
        # Initialize the thread for input command
        if control_mode == 'keyboard':
            self.input_thread = threading.Thread(target=self.listen_input_keyboard, daemon=True)
        elif control_mode == 'mic':
            self.recognizer = sr.Recognizer()
            self.input_thread = threading.Thread(target=self.listen_input_mic, daemon=True)
        self.input_thread.start()
        
        # Initialize the face
        self.enable_face = enable_face
        self.initial_face()
        self.initialize_servos()

    def listen_input_keyboard(self):
        '''
        Listen to the keyboard input.
        '''
        while True:
            self.robot_command = input() 
            print('Get command: {}'.format(self.robot_command))

    def listen_input_mic(self):
        '''
        Listen to the microphone input.
        '''

        with sr.Microphone() as source:
            self.recognizer.adjust_for_ambient_noise(source)
            print("Start listening command...")
            
            while True:
                try:
                    audio_data = self.recognizer.listen(source, timeout=5, phrase_time_limit=10)
                    print("Recognizing...")

                    # if you want to use another language, change the language parameter
                    text = self.recognizer.recognize_google(audio_data, language="en-US") 
                    self.robot_command = text
                    print('Get command: {}'.format(self.robot_command))
                
                except sr.WaitTimeoutError:
                    print("No voidce input detected, please try again!")
                except sr.UnknownValueError:
                    print("Cannot recognize the voice, please try again!")
                except sr.RequestError as e:
                    print(f"Voice recognition service error: {e}")

    def initial_face(self):
        '''
        Initialize the face.
        '''
        if not self.enable_face:
            return
        
        # Set the display, ':0' for Raspberry Pi touch screen
        os.environ["DISPLAY"] = ":0" 
        pygame.init()
        pygame.mouse.set_visible(False)
        self.screen = pygame.display.set_mode((480, 320), pygame.FULLSCREEN)
        pygame.display.set_caption("Face")
        self.BLACK = (0, 0, 0)
        self.WHITE = (255, 255, 255)

        # Load the face images
        self.face_folder = "face"
        self.face_images = {}
        if os.path.exists(self.face_folder):
            for filename in os.listdir(self.face_folder):
                if filename.lower().endswith(('.png', '.jpg', '.jpeg', '.bmp', '.gif')):
                    image_path = os.path.join(self.face_folder, filename)
                    image = pygame.image.load(image_path)
                    image = pygame.transform.scale(image, (480, 320))
                    emotion = filename.split('.')[0]
                    self.face_images[emotion] = image

        # Set the current and backup emotion
        self.current_emotion = 'sleep'
        self.backup_emotion = 'neutral'
        self.show_face()

    def show_face(self):
        '''
        Show the face.
        '''
        if not self.enable_face:
            return
        # Fill the screen with black
        self.screen.fill(self.BLACK)

        # Show the corresponding face image
        self.screen.blit(self.face_images[self.current_emotion], (0, 0))

        # Update the display
        pygame.display.flip()
        
        # Save the current emotion as the backup emotion
        self.backup_emotion = self.current_emotion

    def initialize_servos(self):
        # Initialize the servos
        try:
            self.servos = [LX16A(i) for i in range(1,self.servo_num + 1)]
            for i in range(self.servo_num):
                # Set the limits for the servos
                self.servos[i].set_angle_limits(self.angle_lower_limit, self.angle_upper_limit)
                self.servos[i].set_vin_limits(self.voltage_lower_limit, self.voltage_upper_limit)
                self.servos[i].set_temp_limit(self.temperature_limit)
                self.servos[i].set_led_error_triggers(True, True, True)
                self.servos[i].led_power_on()
                self.servos[i].enable_torque()
        except ServoTimeoutError as e:
            print(f"Servo {e.id_} is not responding. Exiting...")
            quit()
        time.sleep(self.mian_proceed_time)

    def set_all_servos(self,move_time=0,skip=[]):
        '''
        Set all the servos to the target angles.
        
        Args:
            move_time (float): time for moving to the target angles
            skip (list): list of servos to skip
            '''
        assert self.servo_num == len(self.q)
        for i in range(len(self.q)):
            if i in skip:
                continue
            self.servos[i].move(self.q[i],move_time)
    
    def self_check(self):
        '''
        Check the status of the robot.
        '''
        for i in range(self.servo_num):
            # Get the status of the servos.
            self.servo_status[i] = self.servos[i].get_led_error_triggers(True)

            # If the temperature is too high, the voltage is abnormal, or the servo is rocked, print the warning message.
            if self.servo_status[i][0]:
                print(f'Servo {i+1} tempreture is too high!')
            if self.servo_status[i][1]:
                print(f'Servo {i+1} voltage is abnormal!')
            if self.servo_status[i][2]:
                print(f'Servo {i+1} is rocked!')

        if any(True in row for row in self.servo_status):
            raise ServoError('The robot is not working properly! Time: {:.2f}'.format(self.running_time))
        else:    
            print('The robot is working properly! Time: {:.2f}'.format(self.running_time))

    def homing(self,skip=[]):
        '''
        Move the robot to the homing pose.
        '''
        self.q = deepcopy(self.pose_homing)
        self.set_all_servos(self.mian_proceed_time * 1000,skip=skip)
        time.sleep(self.mian_proceed_time + 1)
        print('Successfully move to homing pose! Time: {:.2f}'.format(self.running_time))
    
    def stand_up(self,skip=[]):
        '''
        Move the robot to the standing up pose.
        '''
        self.q = deepcopy(self.pose_stand_up)
        self.set_all_servos(self.mian_proceed_time * 1000,skip=skip)
        time.sleep(self.mian_proceed_time + 1)
        print('Successfully stand up! Time: {:.2f}'.format(self.running_time))

    def nod_head(self):
        '''
        Nod the head.
        '''
        self.servos[6].move(sin(self.timer1) * 15 + 100)

    def prepare_squat(self, squat_ratio = 0.6, squat_frequency = 2):
        '''
        Prepare the squat.
        
        Args:
            squat_ratio (float): squat ratio
            squat_frequency (float): squat frequency
        '''

        # Calculate the difference between the stand up pose and the homing pose
        old_difference = [self.pose_stand_up[i]-self.pose_homing[i] for i in range(self.servo_num)]
        # Calculate the squat pose with the squat ratio
        down = [self.pose_stand_up[i]-old_difference[i] * squat_ratio for i in range(self.servo_num)]

        # Calculate the squatting difference, middle, and frequency
        self.squating_frequency = squat_frequency
        self.squating_difference = [(self.pose_stand_up[i]-down[i])/2 for i in range(self.servo_num)]
        self.squating_middle = [(self.pose_stand_up[i]+down[i])/2 for i in range(self.servo_num)]

    def squat(self,skip=[]):
        '''
        Squat the robot.

        Args:
            skip (list): list of servos to skip
        '''
        self.q = [self.squating_difference[i]*cos(self.squating_frequency*self.timer2) + self.squating_middle[i] for i in range(self.servo_num)]
        self.set_all_servos(skip=skip)

    def prepare_step(self,step_period = 0.4):
        '''
        Prepare the step.
        
        Args:
            step_period (float): step period
        '''
        self.step_period = step_period
        self.step_ferq = 2 * np.pi / step_period
        pose_left_up = [112.32, 111.60, 96.96, 116.88, 108.00, 143.28, 100]
        pose_right_up = [112.32, 125, 105.80, 116.88, 116.40, 153.36, 100]

        self.step_middle_left = [(pose_left_up[i]+self.pose_stand_up[i])/2 for i in range(self.servo_num)]
        self.step_middle_right = [(pose_right_up[i]+self.pose_stand_up[i])/2 for i in range(self.servo_num)]

        self.step_difference_left = [(self.pose_stand_up[i]-pose_left_up[i])/2 for i in range(self.servo_num)]
        self.step_difference_right = [(self.pose_stand_up[i]-pose_right_up[i])/2 for i in range(self.servo_num)]

    def step(self,skip=[6]):
        self.q[1] = self.step_difference_left[1]*cos(self.step_ferq*self.timer2) + self.step_middle_left[1]
        self.q[2] = self.step_difference_left[2]*cos(self.step_ferq*self.timer2) + self.step_middle_left[2]
        if self.timer2 >= self.step_period/2:
            self.q[4] = self.step_difference_right[4]*cos(self.step_ferq*(self.timer2-self.step_period/2)) + self.step_middle_right[4]
            self.q[5] = self.step_difference_right[5]*cos(self.step_ferq*(self.timer2-self.step_period/2)) + self.step_middle_right[5]
        
        self.set_all_servos(skip=skip)

    def prepare_walk(self, walk_period = 0.8):
        '''
        Prepare the walk.
        
        Args:
            walk_period (float): walk period
        '''
        self.walk_period = walk_period
        # self.walk_pose = {'left_font': {2:130.56, 3:96.96},
        #                   'left_back': {2:111.60, 3:116.88},
        #                   'left_trainsition': {2:111.60, 3:96.96},
        #                   'right_font': {5:97.92, 6:153.84},
        #                   'right_back': {5:119.28, 6:132.24},
        #                   'right_trainsition': {5:116.40, 6:153.36}}
        # Walk pose
        self.walk_pose = {'left_font': {2:132, 3:94},
                          'left_back': {2:112, 3:114},
                          'left_trainsition': {2:112, 3:94},
                          'right_font': {5:98, 6:158},
                          'right_back': {5:118, 6:138},
                          'right_trainsition': {5:118, 6:158}}
        Ts = walk_period/4.0

        # Cubic polynomial for walking
        p2_walk = [self.walk_pose['left_font'][2], self.walk_pose['left_back'][2], self.walk_pose['left_trainsition'][2], self.walk_pose['left_font'][2]]
        p3_walk = [self.walk_pose['left_font'][3], self.walk_pose['left_back'][3], self.walk_pose['left_trainsition'][3], self.walk_pose['left_font'][3]]
        tl_walk = [2*Ts , Ts, Ts]
        
        c2_walk = cubic_polynomial_periodic(p2_walk,tl_walk)
        c3_walk = cubic_polynomial_periodic(p3_walk,tl_walk)
        
        p5_walk = [self.walk_pose['right_back'][5], self.walk_pose['right_trainsition'][5], self.walk_pose['right_font'][5], self.walk_pose['right_back'][5]]
        p6_walk = [self.walk_pose['right_back'][6], self.walk_pose['right_trainsition'][6], self.walk_pose['right_font'][6], self.walk_pose['right_back'][6]]
        tr_walk = [Ts , Ts, 2*Ts]
        c5_walk = cubic_polynomial_periodic(p5_walk,tr_walk)
        c6_walk = cubic_polynomial_periodic(p6_walk,tr_walk)
  
        # Calculate the start velocity and acceleration
        c2_start_velocity = c2_walk[2]
        c2_start_acceleration = 2 * c2_walk[1]
        c3_start_velocity = c3_walk[2]
        c3_start_acceleration = 2 * c3_walk[1]
        c5_start_velocity = c5_walk[2]
        c5_start_acceleration = 2 * c5_walk[1]
        c6_start_velocity = c6_walk[2]
        c6_start_acceleration = 2 * c6_walk[1]

        # In perapre, the end velocity and acceleration are constrained
        p2_prepare = [self.pose_stand_up[2-1], self.walk_pose['left_trainsition'][2], self.walk_pose['left_font'][2]]
        p3_prepare = [self.pose_stand_up[3-1], self.walk_pose['left_trainsition'][3], self.walk_pose['left_font'][3]]
        tl_prepare = [1 * Ts, 1 * Ts]

        p5_prepare = [self.pose_stand_up[5-1],self.walk_pose['right_back'][5]]
        p6_prepare = [self.pose_stand_up[6-1],self.walk_pose['right_back'][6]]
        tr_prepare = [2 * Ts]
        self.walk_prepare_time = sum(tl_prepare)
        
        c2_prepare = cubic_polynomial(p2_prepare,tl_prepare,c2_start_velocity,c2_start_acceleration,constraint_type='end')
        c3_prepare = cubic_polynomial(p3_prepare,tl_prepare,c3_start_velocity,c3_start_acceleration,constraint_type='end')
        c5_prepare = cubic_polynomial(p5_prepare,tr_prepare,c5_start_velocity,c5_start_acceleration,constraint_type='end')
        c6_prepare = cubic_polynomial(p6_prepare,tr_prepare,c6_start_velocity,c6_start_acceleration,constraint_type='end')

        # In stop, the start velocity and acceleration are constrained
        p2_stop = [self.walk_pose['left_font'][2],self.pose_stand_up[2-1]]
        p3_stop = [self.walk_pose['left_font'][3],self.pose_stand_up[3-1]]
        tl_stop = [2 * Ts]

        p5_stop = [self.walk_pose['right_back'][5],self.walk_pose['right_trainsition'][5],self.pose_stand_up[5-1]]
        p6_stop = [self.walk_pose['right_back'][6],self.walk_pose['right_trainsition'][6],self.pose_stand_up[6-1]]
        tr_stop = [1 * Ts, 1 * Ts]
        self.walk_stop_time = sum(tr_stop)

        c2_stop = cubic_polynomial(p2_stop,tl_stop,c2_start_velocity,c2_start_acceleration,constraint_type='start')
        c3_stop = cubic_polynomial(p3_stop,tl_stop,c3_start_velocity,c3_start_acceleration,constraint_type='start')
        c5_stop = cubic_polynomial(p5_stop,tr_stop,c5_start_velocity,c5_start_acceleration,constraint_type='start')
        c6_stop = cubic_polynomial(p6_stop,tr_stop,c6_start_velocity,c6_start_acceleration,constraint_type='start')

        # Save the cubic polynomial coefficients
        self.curve_properties[1] = {'cubic_walk': c2_walk, 'time_stamp': np.cumsum(tl_walk),
                                     'cubic_prepare': c2_prepare, 'time_stamp_prepare': np.cumsum(tl_prepare),
                                     'cubic_stop': c2_stop, 'time_stamp_stop': np.cumsum(tl_stop)}
        self.curve_properties[2] = {'cubic_walk': c3_walk, 'time_stamp': np.cumsum(tl_walk),
                                     'cubic_prepare': c3_prepare, 'time_stamp_prepare': np.cumsum(tl_prepare),
                                     'cubic_stop': c3_stop, 'time_stamp_stop': np.cumsum(tl_stop)}
        self.curve_properties[4] = {'cubic_walk': c5_walk, 'time_stamp': np.cumsum(tr_walk),
                                     'cubic_prepare': c5_prepare, 'time_stamp_prepare': np.cumsum(tr_prepare),
                                     'cubic_stop': c5_stop, 'time_stamp_stop': np.cumsum(tr_stop)}
        self.curve_properties[5] = {'cubic_walk': c6_walk, 'time_stamp': np.cumsum(tr_walk),
                                    'cubic_prepare': c6_prepare, 'time_stamp_prepare': np.cumsum(tr_prepare),
                                    'cubic_stop': c6_stop, 'time_stamp_stop': np.cumsum(tr_stop)}

        
    def walk(self,skip=[6]):
        '''
        Walk the robot.
        
        Args:
            skip (list): list of servos to skip
        '''
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

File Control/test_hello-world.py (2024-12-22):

from math import sin, cos
from pylx16a.lx16a import *
import time

# change "/COM6" to the port where the LX-16A is connected
LX16A.initialize("/COM6", 0.1)

try:
    servo1 = LX16A(1)
    servo2 = LX16A(2)
    servo3 = LX16A(3)
    servo1.set_angle_limits(0, 240)
    servo2.set_angle_limits(0, 240)
    servo3.set_angle_limits(0, 240)
except ServoTimeoutError as e:
    print(f"Servo {e.id_} is not responding. Exiting...")
    quit()

t = 0
# give enough time for servo to initialization
time.sleep(3)
# move to start position
servo1.move(120,2000)
servo2.move(120,2000)
servo3.move(120,2000)
time.sleep(3)
while True:
    servo1.move(sin(t) * 20 + 120)
    servo2.move(sin(t) * 20 + 120)
    servo3.move(sin(t) * 20 + 120)

    time.sleep(0.05)
    t += 0.1

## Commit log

2024-12-22 12/12/22 11:06 Update
    [Base_Modulous.STL, Base_Platform.STL, Battery_Holder.STL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]
2024-12-22 12/12/22 11:06 Update 3
    [Fake_Shoulder_Screw_16_type1.STL, Fake_Shoulder_Screw_16_type2.STL, Fake_Shoulder_Screw_25_type1.STL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]
2024-12-23 12/22/2024 21:46 Update
    [Fake_Shoulder_Screw_16_type1.STL, Fake_Shoulder_Screw_16_type2.STL, Fake_Shoulder_Screw_25_type1.STL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]
2024-12-23 12/22/2024 22:51 Update
    [Left_Feet.STL, Left_Lower.STL, Left_Upper.STL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]
2024-12-23 12/22/2024 23:13 Update
    [Robot.3mf]
2025-09-29 Clarify motor usage impact on robot weight
    Updated wording for clarity regarding motor usage.
